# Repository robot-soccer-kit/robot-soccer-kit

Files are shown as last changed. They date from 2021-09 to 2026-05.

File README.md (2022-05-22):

# Robot Soccer Kit

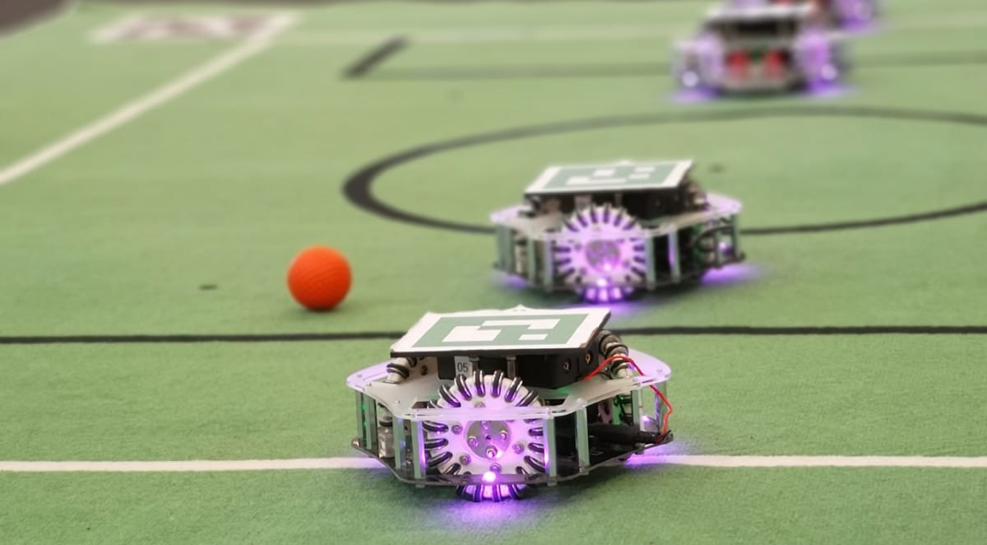
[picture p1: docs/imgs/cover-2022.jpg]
Robots


## Presentation

* [YouTube demonstration video](https://www.youtube.com/watch?v=4NFXbaom7YQ)
* [Documentation](https://robot-soccer-kit.github.io)

## License

<br />This work is licensed under a <a rel="license" href="http://creativecommons.org/licenses/by-nc/2.0/">Creative Commons Attribution-NonCommercial 2.0 Generic License</a>.

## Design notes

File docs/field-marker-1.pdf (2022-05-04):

## Marker 1

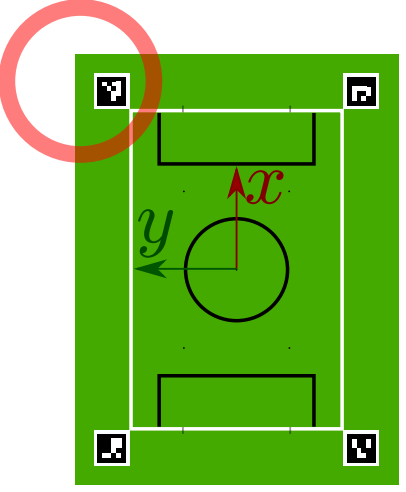
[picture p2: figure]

## WARNING

Use the same position and
orientation as on the picture

Keep ~2.5 cm of white around the marker

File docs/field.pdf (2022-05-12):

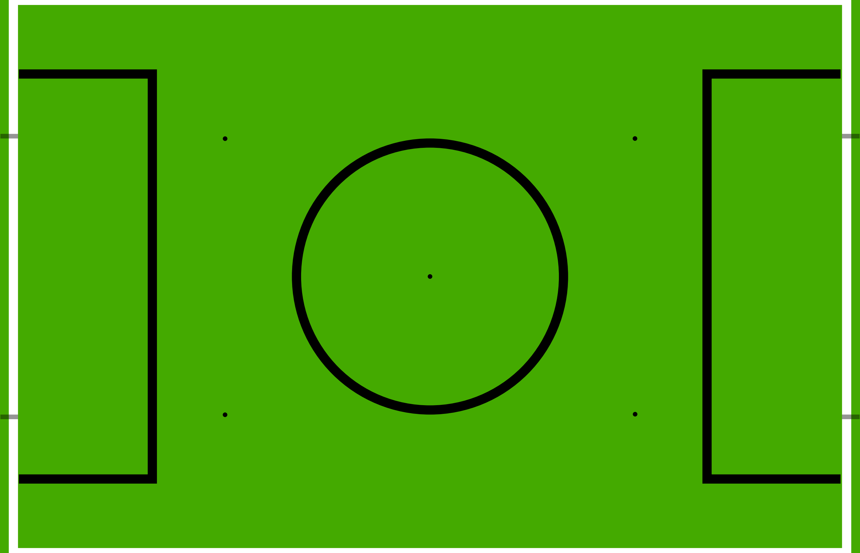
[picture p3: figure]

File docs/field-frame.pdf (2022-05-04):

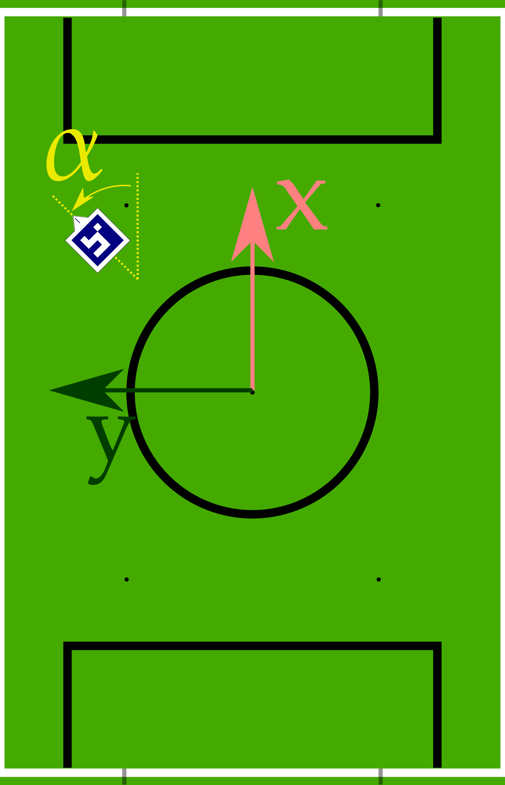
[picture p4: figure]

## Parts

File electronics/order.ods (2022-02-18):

Item # | Ref | Qty | Manufacturer | Mfg Part # | Description | Package | Type | Instruction
1 | B1 | 1 |  |  | BUZZER66 |  |  | CEM-1203
2 | C1, C2, C3, C4, C5, C6, C7, C8 | 8 |  |  | 0.1µF |  |  | 2688486RL
3 | C10, C11 | 2 |  |  | 47pF |  |  | 1081223
4 | C15, C16 | 2 |  |  | 22uF |  |  | 2666560
5 | C19, C20 | 2 |  |  | 2200uF |  |  | 1902893
6 | D1 | 1 |  |  | PMEG4030EP |  |  | 1829201
7 | D3 | 1 |  |  |  |  |  | 8737843RL
8 | J1 | 1 |  |  | USB-B |  |  | 1308876
9 | J2 | 1 |  |  |  |  |  | 1217037
10 | J3, J4, J5 | 3 |  |  | B6B-ZR |  |  | 9491805
11 | J6 | 1 |  |  | KICKER |  |  | JF-0530B
12 | L1 | 1 |  |  | IHLP2525CZER220M11IND_IHLP_2525_CZ_VIS-M |  |  | 1741369
13 | LED1, LED2, LED3, LED4, LED5, LED6 | 6 |  |  | WS2812B5050 |  |  | WS2812B 5050
14 | Q1, Q2 | 2 |  |  | IRLMS2002TRPBF |  |  | 2577180RL
15 | Q3 | 1 |  |  | NPN_BC817,215 |  |  | 1081223
16 | Q4 | 1 |  |  | SUD50N04-8M8P-4GE3 |  |  | 1794799
17 | R1 | 1 |  |  | 270 |  |  | 1887603
19 | R3 | 1 |  |  | 20K |  |  | 2074395
20 | R4 | 1 |  |  | 68k |  |  | 2447023
21 | R5, R9, R10 | 3 |  |  | 10K |  |  | 2074334RL
22 | R6 | 1 |  |  | 3K |  |  | 2447648
23 | R7 | 1 |  |  | 470 |  |  | 2447662
24 | R2, R8, R11 | 3 |  |  | 2K |  |  | 2447622
25 | R12, R13 | 2 |  |  | 22 |  |  | 2446926
26 | REG1 | 1 |  |  | REG 3.3V |  |  | 3470633
 | REG2 | 1 |  |  | REG 5V |  |  | 3470634
27 | S1 | 1 |  |  | DPDT |  |  | 2435159
28 | U1 | 1 |  |  | FT232L |  |  | 1146032
29 | U2 | 1 |  |  | ESP32-WROOM-32E_(16MB) |  |  | ESP32-WROOM
30 | U3 | 1 |  |  | S8252 |  |  | https://www.digikey.fr/fr/products/detail/ablic-u-s-a-inc/S-8252AAL-M6T1U/6121452
31 | U4, U5, U6 | 3 |  |  | L9110 |  |  | L9110 SOIC8
32 | U7 | 1 |  |  | MT3608 |  |  | MT3608

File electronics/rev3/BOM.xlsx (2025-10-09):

Item # | Ref | Qty | Manufacturer | Mfg Part # | Description | Package | Type | Instruction
1 | R2 | 1 | MULTICOMP PRO | MCSR08X2001FTL | 2k ohms | R0805 | SMD
2 | R3 | 1 | MULTICOMP PRO | MCSR08X2002FTL | 20k ohms | R0805 | SMD
3 | R4, R18 | 2 | MULTICOMP PRO | MCWR08X6802FTL | 68k ohms | R0805 | SMD
4 | R1, R5, R16, R17 | 4 | MULTICOMP PRO | MCSR08X1002FTL | 10k ohms | R0805 | SMD
5 | R6 | 1 | MULTICOMP PRO | MCWR08X3001FTL | 3k ohms | R0805 | SMD
6 | R7, R9, R10 | 3 | MULTICOMP PRO | MCWR08X4700FTL | 470 ohms | R0805 | SMD
7 | R8, R11 | 2 | MULTICOMP PRO | MCWR08X2001FTL | 2k ohms | R0805 | SMD
8 | R12, R13 | 2 | MULTICOMP PRO | MCWR08X22R0FTL | 22 ohms | R0805 | SMD
9 | R15, R22 | 2 | MULTICOMP PRO | MCWR08X5101FTL | 5.1k ohms | R0805 | SMD
10 | R14 | 1 | MULTICOMP PRO | MCPWR10FTEQ2700 | Kicker resistor (270) | R2010 | SMD
11 | R19 , R20, R21 | 3 | VISHAY | RCWE0805R330FKEA | 330 mOhms | R0805 | SMD
12 | C13, C17, C18, C21, C22 | 5 | MURATA | GCM21BR71E105KA56L | 1µF | C0805 | SMD
13 | C1, C2, C3, C4, C5, C6, C7, C8, C9, C12, C14 | 11 | MURATA | GCM21BR72A104KA37K | 0.1µF | C0805 | SMD
14 | C10, C11 | 2 | MULTICOMP PRO | MC0805N470J500CT | 47pF (USB) | C0805 | SMD
15 | C15, C16 | 2 | MURATA | GRM21BR61E226ME44L | 22uF (Booster) | C0805 | SMD
16 | C19, C20 | 2 | WURTH ELEKTRONIK | 860020478022 | 2200uF 25V capacitors (Kicker) |  | Thru-holes
17 | D1 | 1 | NEXPERIA | PMEG4030EP,115 | Kicker diode | SOD-128 | SMD
18 | D2, D3 | 2 | NEXPERIA | PMEG2005AEA,115 | USB diode, BMS bootstrap polarity protection diode | SOD-323 | SMD
19 | B1 | 1 | CUI Devices | CEM-1203 | Buzzer |  | Thru-holes
20 | J1 | 1 | MULTICOMP PRO | USB-B-S-RA | USB Connector |  | Thru-holes
21 | J2 | 1 | MULTICOMP PRO | MJ-180PH | Jack 2.5mm « barrel » connector |  | Thru-holes
22 | J3, J4, J5 | 3 | JST (JAPAN SOLDERLESS TERMINALS) | B6B-ZR(LF)(SN) | JST XH 6p |  | Thru-holes
23 | J6 | 1 |  | JF-0530B | Solenoid Kicker |  | SMD | DO NOT MOUNT
24 | L1 | 1 | VISHAY | IHLP2525CZER220M11 | Kicker booster inductance |  | SMD
25 | LED1, LED2, LED3, LED4, LED5, LED6 | 6 | SparkFun | COM-16346 | RGB LEDs (WS2812B) |  | SMD
26 | Q1, Q2, Q7 | 3 | INFINEON | IRLMS2002TRPBF | BMS Mosfet |  | SMD
27 | Q3, Q5, Q6 | 3 | NEXPERIA | BC817,215 | NPN Transistor |  | SMD
28 | Q4 | 1 | MCC (MICRO COMMERCIAL COMPONENTS) | MCU60N04A-TP | Kicker MOSFET |  | SMD
29 | REG1 | 1 | TRACO POWER | TSR 1-2450E | 5V regulator (switching) |  | Thru-holes
30 | U8 | 1 | ANALOG DEVICES | LT1963AEST-3.3#PBF | 3.3V regulator (LDO) |  | SMD
31 | SW1 | 1 | C&K COMPONENTS | L102011ML04Q | Main switch (SPDT) |  | Thru-holes
32 | U1 | 1 | FTDI | FT232RL-REEL | USB 2 UART (FTDI) |  | SMD
33 | U2 | 1 | ESPRESSIF SYSTEMS | ESP32-WROOM-32E-N8 | MCU ESP32 |  | SMD
34 | U3 | 1 | ABLIC Inc. | S-8252AAL-M6T1U | BMS |  | SMD
35 | U10, U11, U12 | 3 | TOSHIBA | TB67H450FNG,EL | H-bridge | SOP8 | SMD
36 | U7 | 1 | AEROSEMI | MT3608 | Step-up Booster 20V |  | SMD
37 | D4 | 1 | ONSEMI | RS1M | Kicker free wheel diode |  | SMD

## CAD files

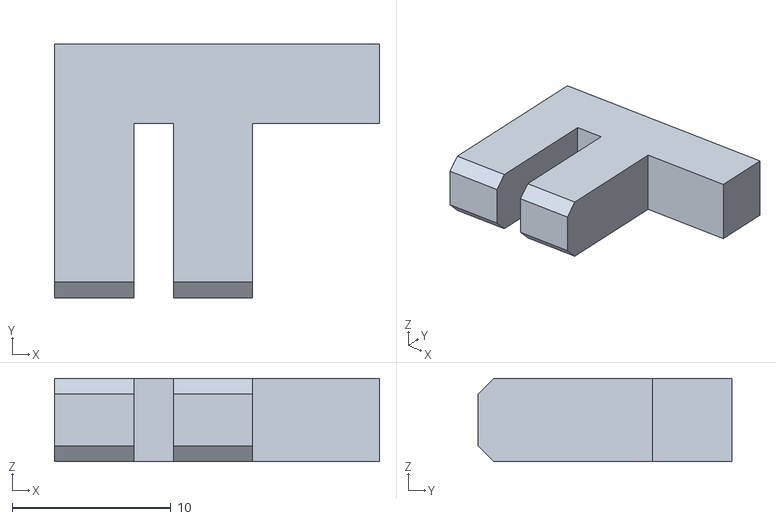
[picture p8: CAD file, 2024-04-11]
mechanics/blocker.stl
20.5 x 16.0 x 5.25

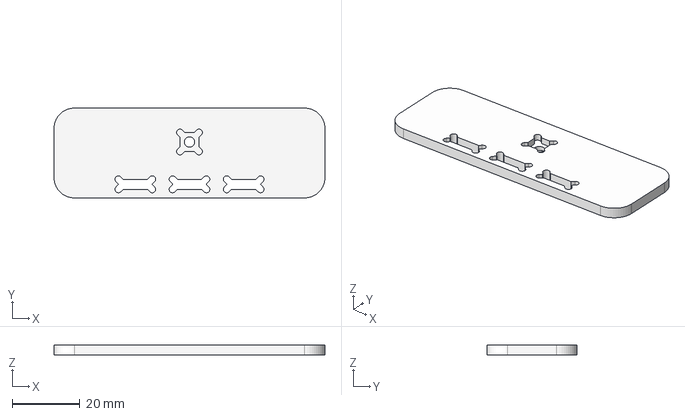
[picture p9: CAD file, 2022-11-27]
mechanics/kicker_tip_1.step
80.0 x 26.5 x 3.00 mm

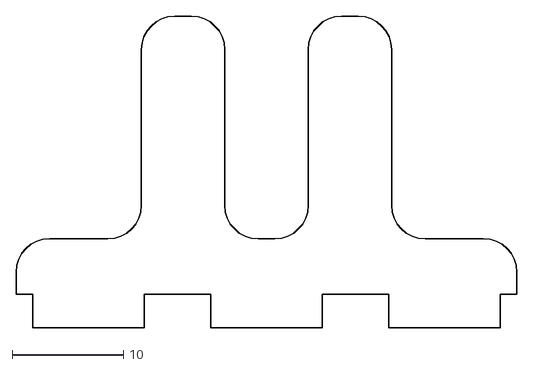
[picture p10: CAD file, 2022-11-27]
mechanics/kicker_tip_2.dxf
45.0 x 28.0

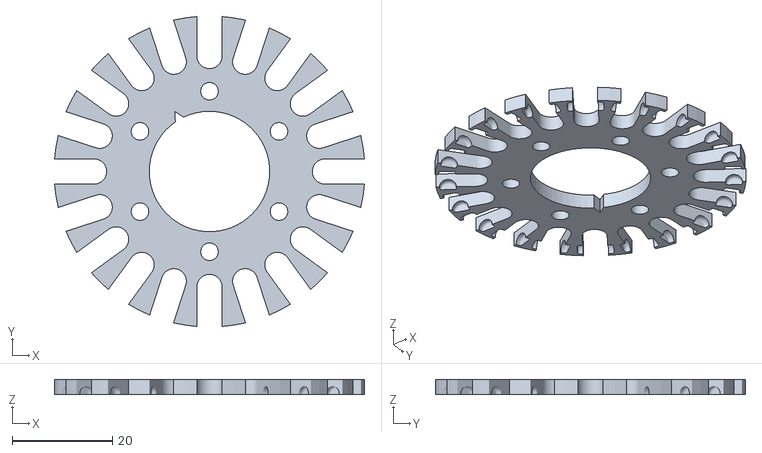
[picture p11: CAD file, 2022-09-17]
mechanics/wheel2.stl
61.8 x 61.8 x 3.00

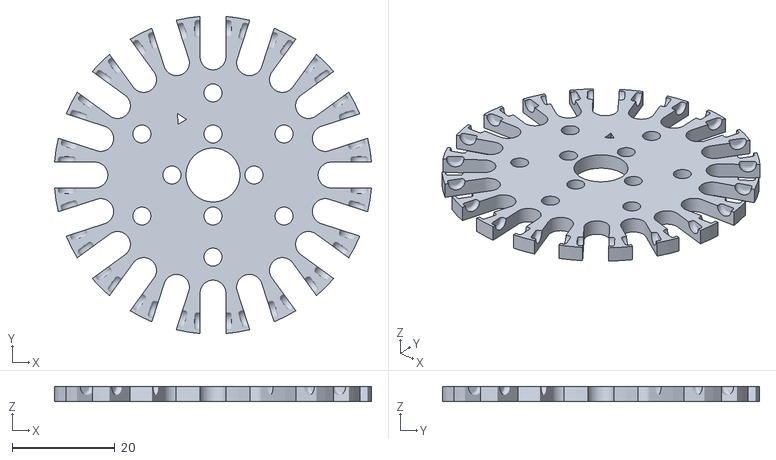
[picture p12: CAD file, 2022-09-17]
mechanics/wheel1.stl
61.8 x 61.8 x 3.00

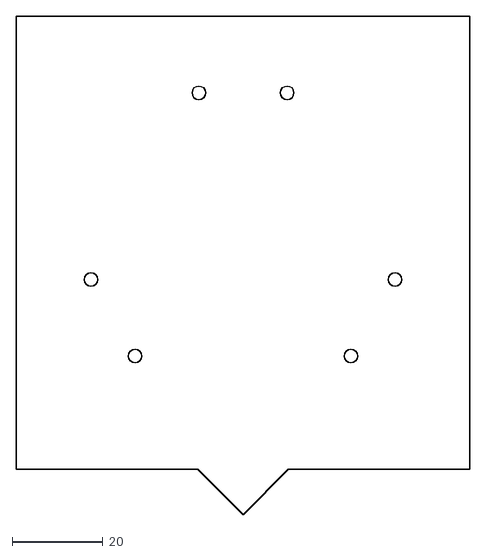
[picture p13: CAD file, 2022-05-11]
mechanics/marker.dxf
100.0 x 110.0

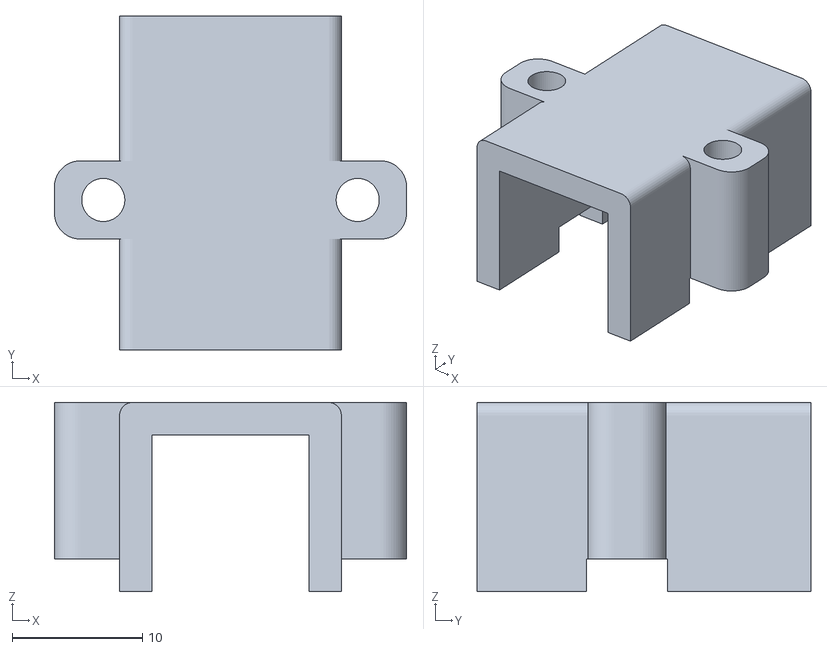
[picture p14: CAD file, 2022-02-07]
mechanics/motorbox_top.stl
27.0 x 25.6 x 14.5

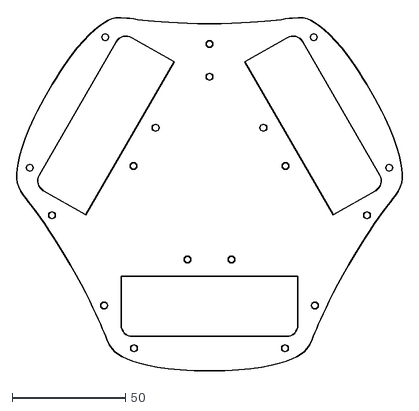
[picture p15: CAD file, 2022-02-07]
mechanics/electronics_board.dxf
170.6 x 156.5

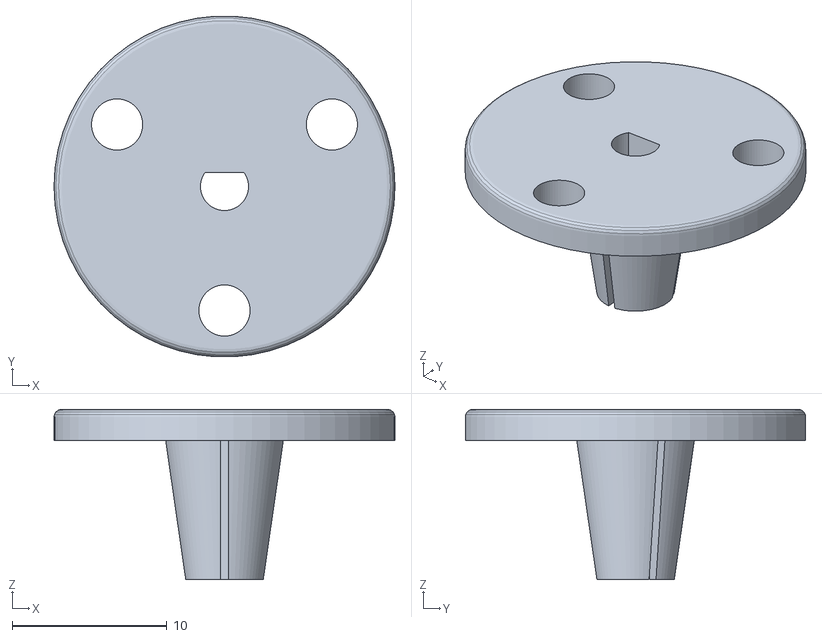
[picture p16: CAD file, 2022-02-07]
mechanics/coupler.stl
22.0 x 22.0 x 11.0

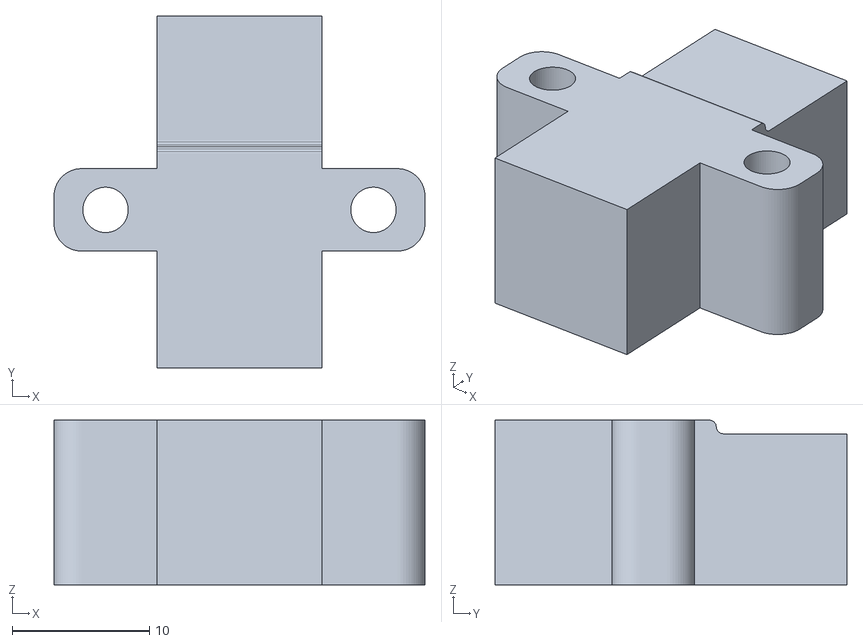
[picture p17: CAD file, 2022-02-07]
mechanics/motorbox_bottom.stl
27.0 x 25.6 x 12.0

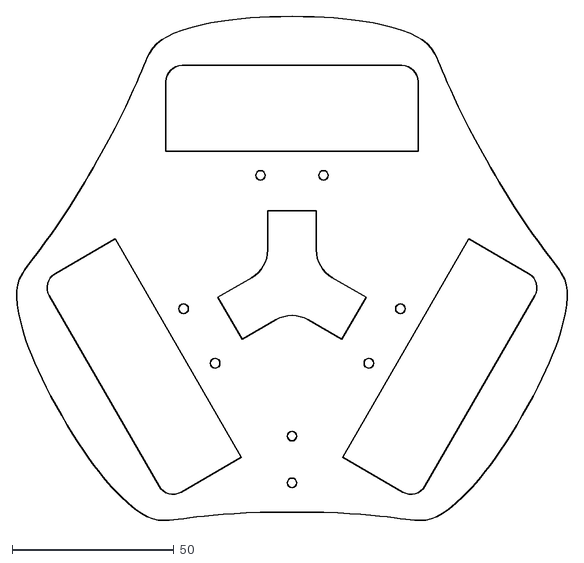
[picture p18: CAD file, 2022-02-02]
mechanics/frame.dxf
170.6 x 156.5

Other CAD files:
mechanics/kicker_tip_1.dxf

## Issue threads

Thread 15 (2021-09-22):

Robots upgrade and rework

Gregwar, 2021-09-22:
Branch `electronics_rework`

- [x] Use 18650 instead of embedded lithium ion (the coupler should fit in current robots)
  - In this move, a way much simpler switch can be used because embedded charge would not be needed anymore
  - Maybe we can have a DC 5.5mm connector and use a coupler
- [x] Get the robot closer to the ground (by ~5mm)
- [x] Remove buttons
- [x] Remove connectors for optical sensors
- [x] Remove distance sensor
- [x] Remove useless multiplexers
- [x] Merge the kicker board to the robot's PCB itself
- [x] Get the robot shielded against collisions (avoid overlap)
- [x] Change the kicker tip (make it wider and more concave)

Ideas / questions
- Can we switch to another reduction ratio ?
- Can we remove the IMU ?
- Should we still use HC-05 or switch to something else ? (Test other bluetooth modules)

Closed 2022-05-04.

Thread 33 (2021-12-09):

When a robot blinks because of battery error and goes back to normal, LED are not re-set to marker's

Gregwar, 2021-12-09:

Closed 2022-05-22.

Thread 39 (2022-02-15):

Electronics rework remarks

Gregwar, 2022-02-15:
- [ ] VM needs to be shorted after battery was plugged

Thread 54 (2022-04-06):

Undefined behavior with the Bluetooth pairing

CoAuToSe, 2022-04-06:
When connecting one of the robots with Bluetooth, the robot almost imediatly change from "connected" to "coupled". Therefore, we can't properly use the robots. The physical setup used is this [one](https://robot-soccer-kit.github.io/hardware-setup) and the software setup is this [one](https://robot-soccer-kit.github.io/install-windows/) (the software is working properly when the robot is "connected" but not "coupled"), meaning that it should be working but it doesn't... We got it working properly about 1 time out of 30 (mainly with a new computer each try but also rarely with one that was already used).

Also, when looking at the Device Manager, the robot is still in the Bluetooth device (even shutdown) and doesn't want to be deleted, but can be deleted when there are multiple robot. (example: I have "holo_6" in my list of Bluetooth devices but the robot "holo_6" is 2 km away from me and is not powered)

OS: Windows 10

Gregwar, 2022-04-06:
Hello,

1. Is there internal Bluetooth in the computers you are using ?
2. If you want to delete a robot, can you try plugging the dongle you used for pair before clicking on "Delete" ?

I am not sure to understand what your problem actually is; do you mean that COM ports opening simply fails?

CoAuToSe, 2022-04-06:
There is internal Bluetooth in the computers we use. We started using it because it was able to "work" but we bought a dongle and nothing changed when using it.
We initially paired the robot with the Bluetooth of our computers and not with the dongle. When we tried to pair them with the dongle, we ran into the same issue.

We can delete the COM ports as much as we want, but I think that the Bluetooth pairing is not working as intended in our case as. We can connect to the robots with Bluetooth without issue (creating the COM ports) but the connection seems to be unstable, usually ending in pairing and not conneting. And, therefore, not allowing us to use the robots.

cgaspard3333, 2022-04-06:
Hello,

We are trying to understand your problem.
Are you a student or a teacher participating to the RSK program in the "Académie de Bordeaux" ?

If so, we can help you with a TeamViewer assistance.
We have the setup fully working with several Computers with Windows 10 and Windows 11 and no real pairing problem (most of the time this sort of problem apears on Linux)

However, using the internal Bluetooth is not really fonctionnal. For now, we strongly recommand to use a dongle.
(It works well with the following dongle referenced in the documentation : ZEXMTE Adaptateur Bluetooth Usb 5.0)
By experiment, Realtek internal Bluetooth seems to work, but Intel is not working well.

Furthermore, **before plugging in the dongle** (and then use it), you have to first disable the internal Bluetooth adapter **in the Device Manager** and not in the Windows Settings interface. Then try to pair again the bots (even they already exist in the device manager)

CoAuToSe, 2022-04-15:
Ok, so I resolved the problem that I was having but it came back later with the dongle, here is how I handled the issues:

1. First, I had the problem with the Bluetooth of the computer taking the lead over the dongle, which may create some Bluetooth ghost linked Robot (which can't be deleted). It was solved by disalbing the Bluetooth of the computer and then plugging in the dongle which may allow the ghost linked robots to be deleted. Otherwise it is the second problem that I resolved.

2. I ran into another problem when coming back to my "old" workspace, about one week without working with it. All the robot's Bluetooth links became ghost on the dongle's Bluetooth and didn't wanted to be deleted(even with the dongle plugged in in the right USB).
To resolve it, I came back to a fresh state of the computer that I was using. I tried deleting Bluetooth links as soon as possible (if u don't use the dongle it may not work, as tested) but there was one ghost robot remaining (and the game controller wasn't working as intended). I might have tried everything that would come to mind quickly to solve this issues.
The solution that I found was to unplug the dongle and reactivate my computer's Bluetooth followed by a restart of the computer (restarting without the computer's Bluetooth reactivated didn't solved the issue for us, shutting down and turning on the computer wasn't tested). Which allowed the deletion of the ghost robot when plugging the dongle (may require to be done "as fast as possible", otherwise you may need to restart "the whole solution"). Therefore it was as if I had never connected the robots to the computer. Following with the steps of the first issue, we currently have it working for us. (even if I had to wait more than a minute "in the void" for the robot to connect with the game controller, with the dongle plugged and a robot linked with the Blutooth)

I also recognised that the dongle may need to be plugged into a USB type charger(the one with the charger icon) of a laptop to have it working. The dongle's LED was blinking more when used this way, and I had more problems otherwise.

The process are long and may be shortened.

To clarify who I am, I am Aurelien from ESME.

Closed 2022-04-30.

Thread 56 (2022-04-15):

Camera calibration

Gregwar, 2022-04-15:
Instead of computing an homography, we could estimate intrinsic+extrinsic camera parameters.
That would give more convenient tool to compute the projection of objects that doesn't lie in the ground plane.

Closed 2022-05-04.

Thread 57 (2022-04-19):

Electronics rev1

Gregwar, 2022-04-19:
- Board should be re-routed: the decoupling capacitor of U5 is too far
- Add 1uF decoupling on H-bridges
- We broke some L9110, but it is likely to come from a bad batch, we might switch to a more reliable H driver

Closed 2022-11-14.

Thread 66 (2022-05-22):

Dispatch to robot to different penalty locations

Gregwar, 2022-05-22:
Currently when a robot is penalized it is just sent to the current X position and the closest border for Y, we could pre-allocate penalty locations around the field and send the robot to the closest unoccupied one, avoiding robots stacking together when penalized

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

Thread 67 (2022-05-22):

Set a limit of time between 2 kicks

Gregwar, 2022-05-22:
In the firmware, that would ensure capacitors reloaded before kicking again. Since it doesn't look like to damage anything that is not affecting the games that much so far though and is debatable.

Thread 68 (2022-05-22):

Removing penalties when placing the robots?

Gregwar, 2022-05-22:
Currently, when there is a lack of progress, we click "Pause" and then "Standard" and then "Resume"; but this doesn't remove the robots penalties (as an effect, the robot goes back to its penalized area after placing)

I suggest that clicking "Standard" remove the robots penalties, since I think it would solve this use case and doesn't seems to affect other use cases.

Closed 2022-11-14.

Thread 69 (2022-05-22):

Swapping covers robots placement

Gregwar, 2022-05-22:
We don't know if the robots finished their placing when swapping covers, it can happen that they didn't and taking their cover in this situation is very annoying

I don't know what to do to solve this, maybe having a way to know if they are moving or ready to swap (LEDs?)

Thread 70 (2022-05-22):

Client exceptions management

Gregwar, 2022-05-22:
Client exceptions `ClientError` are currently raised when:
1. The key is bad
2. The team is not allowed to control robots
3. The robot is preempted
4. The robot is penalized (which is actually a sub-case of preempted)

Cases 1., 2. and 3.+4. should be easily programmatically distinguishable using maybe a different exception.

Also, since most teams simply ignore the errors with a `pass` (at least when preempted/penalized), it should be possible to simply silently ignore them, for instance `client.raise_exceptions = False` to disable exceptions for cases 2.+3.+4.

I think case 1. should always raise though.

Maybe we should have 3 levels instead, like `client.error_management = "..."`, with `"ignore"`, `"print"` and `"raise"` (default: print)

Gregwar, 2022-06-07:
If we disable exception, we could call it yoda mode :-)

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

Closed 2023-04-07.

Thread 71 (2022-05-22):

Robot restarts when opening connection

Gregwar, 2022-05-22:
Sometime when opening the connection with robots, they restart. We are not sure yet why this happens. It is not causing a big problem since when the connection is successful we didn't observe any problem during the competition.

Observed from Ubuntu 22.04 main computer.

Here are some hypotheses but the problem needs to be reproduced and investigated further:
- Maybe it is because the batteries voltage is too high (+8V) and the BMS over-voltage shut-down
- Maybe it is because something is trying to send orders to the robot (tasks or clients through API) at the same time

Gregwar, 2022-11-14:
Duplicates #86

Closed 2022-11-14.

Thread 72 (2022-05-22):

Timer should be reset to 05:00 before we click on Resume

Gregwar, 2022-05-22:
Currently it shows the timer from the previous game, and only resets to 05:00 when game actually starts

Closed 2023-04-07.

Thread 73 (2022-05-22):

Kickers seems irregular from robot to robot

Gregwar, 2022-05-22:
We need to investigate on what makes some robot kicking differently

Leads
- Different Solenoid
- Different mechanics (frictions?)
- Different capacitors
- Different power MOS

We can assemble/disassemble and benchmark, very tedious way to the truth of what really matters here

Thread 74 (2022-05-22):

Robots can't push the ball and can still climb the ball

Gregwar, 2022-05-22:
When the robot move straightfoward to the ball, the kicker gets a little stuck on it. It is not point of the games to push the ball because we want to encourage kicking, but it is still not some behaviour we want.

The kicker is looking "downward" on current builds, we could use a M3 nut to get it looking "upward", we think it would fix this.

Also, the robots can still climb the ball on some situation, maybe the distance between PCB and the ground can be again reduced a little bit.

Gregwar, 2022-11-14:
We think this is caused by the front square nut in the kicker. Should be fixed in design now (to test).

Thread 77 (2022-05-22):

Goals and sideline crossed

Gregwar, 2022-05-22:
In the current code it is possible that both a goal and a sideline crossed is detected simultaneously, it should be exclusive

(Fixed but not commited)

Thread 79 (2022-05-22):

Get wheel closer to motor bearing

Gregwar, 2022-05-22:
Looks like some motors got broken because of radial effort.
The wheels could be mounted closer to the bearing, we think each mm would help reducing this effort. Maybe the wheel can be mounted "inside" the coupler, but we need to be able to access the headless screw for assembling.

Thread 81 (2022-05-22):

Limit motors that force for no result

Gregwar, 2022-05-22:
We don't have temperature feedback, but measure the speed and know the PWM signal used.
If the speed is highly inconsistent with the PWM signal used for too long, we might have some process to stop forcing.

(Maybe a metric like robot "stamina" could be used, to give an incentive to avoid forcing and pushing, and also avoid breaking the motors.)

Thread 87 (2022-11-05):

R19, R20, R21 are not consistent with BOM

Gregwar, 2022-11-05:
R19, R20, R21 (330mOhms) are not consistent between CAD and BOM
BOM is stating R0805 resistors but this is not the package used in the CAD

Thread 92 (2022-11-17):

LEDs and Buzzer in API

Gregwar, 2022-11-17:
- It should be possible, but not during games

Closed 2023-04-07.

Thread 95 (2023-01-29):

Slight adjustements in dimensions

Gregwar, 2023-01-29:
After the last batch, we can slightly adjust:

- [ ] The holes for the upper PMMA plate could be enlarged so that it is less adjusted
- [ ] The holes in the motor box can be enlarged a little bit; the SLS stack pillars sometime fused with it

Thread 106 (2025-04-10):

Timed circle delay

Gregwar, 2025-04-10:
If ball is not seen for a frame, timer seems to be reset
To investigate

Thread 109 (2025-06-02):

Improve robot penalty placement

Gregwar, 2025-06-02:
Currently, the robots often hamper the game when going to penalty spot

Proposal: instead of minimizing distance to penalty spot, avoid intersecting obstacles

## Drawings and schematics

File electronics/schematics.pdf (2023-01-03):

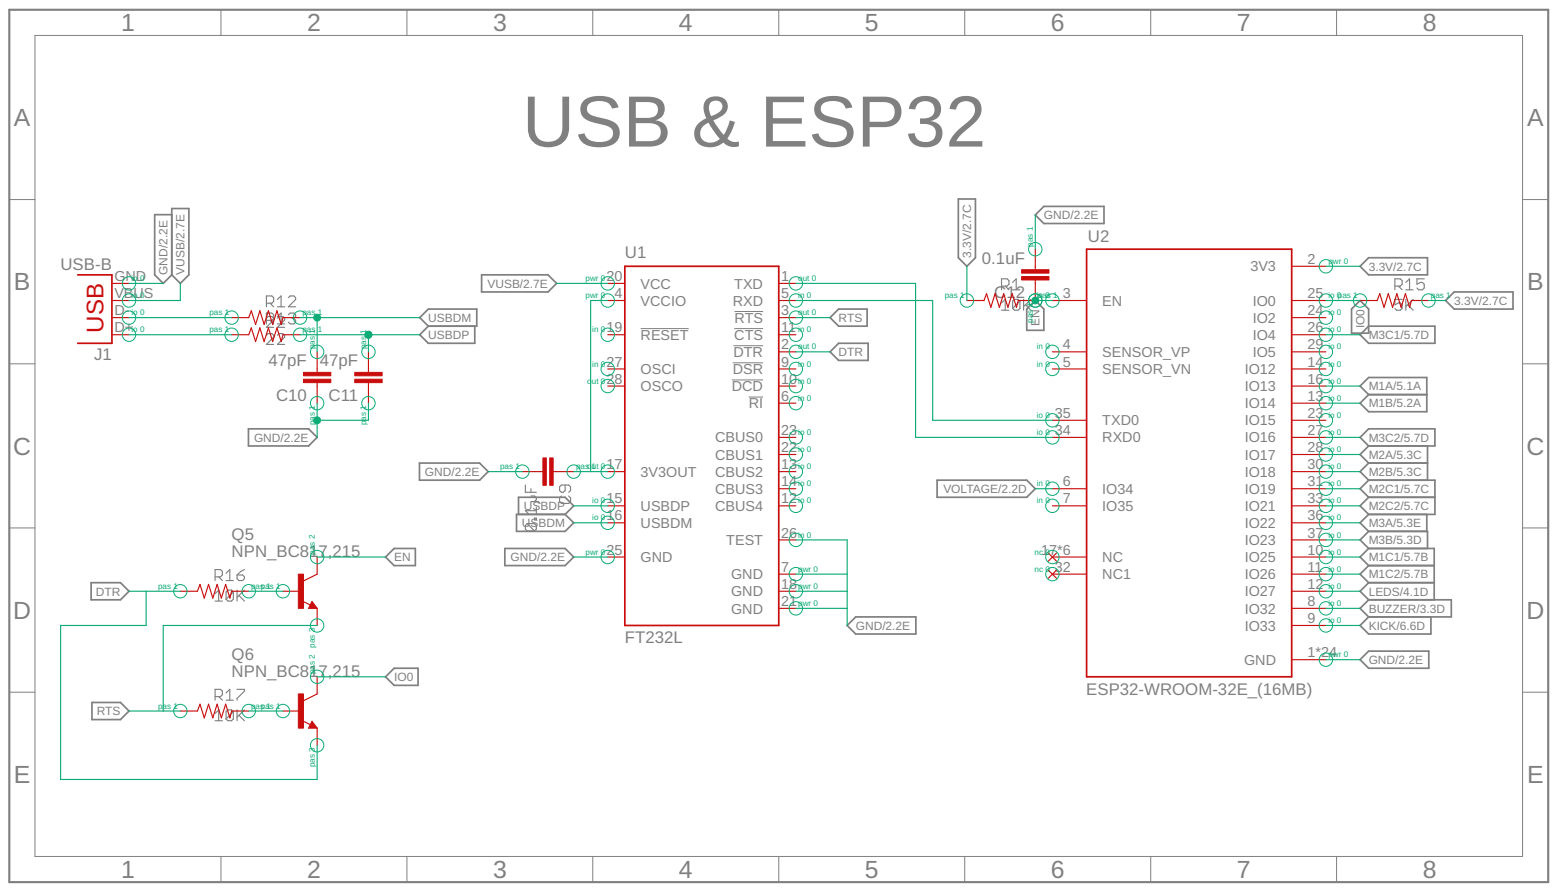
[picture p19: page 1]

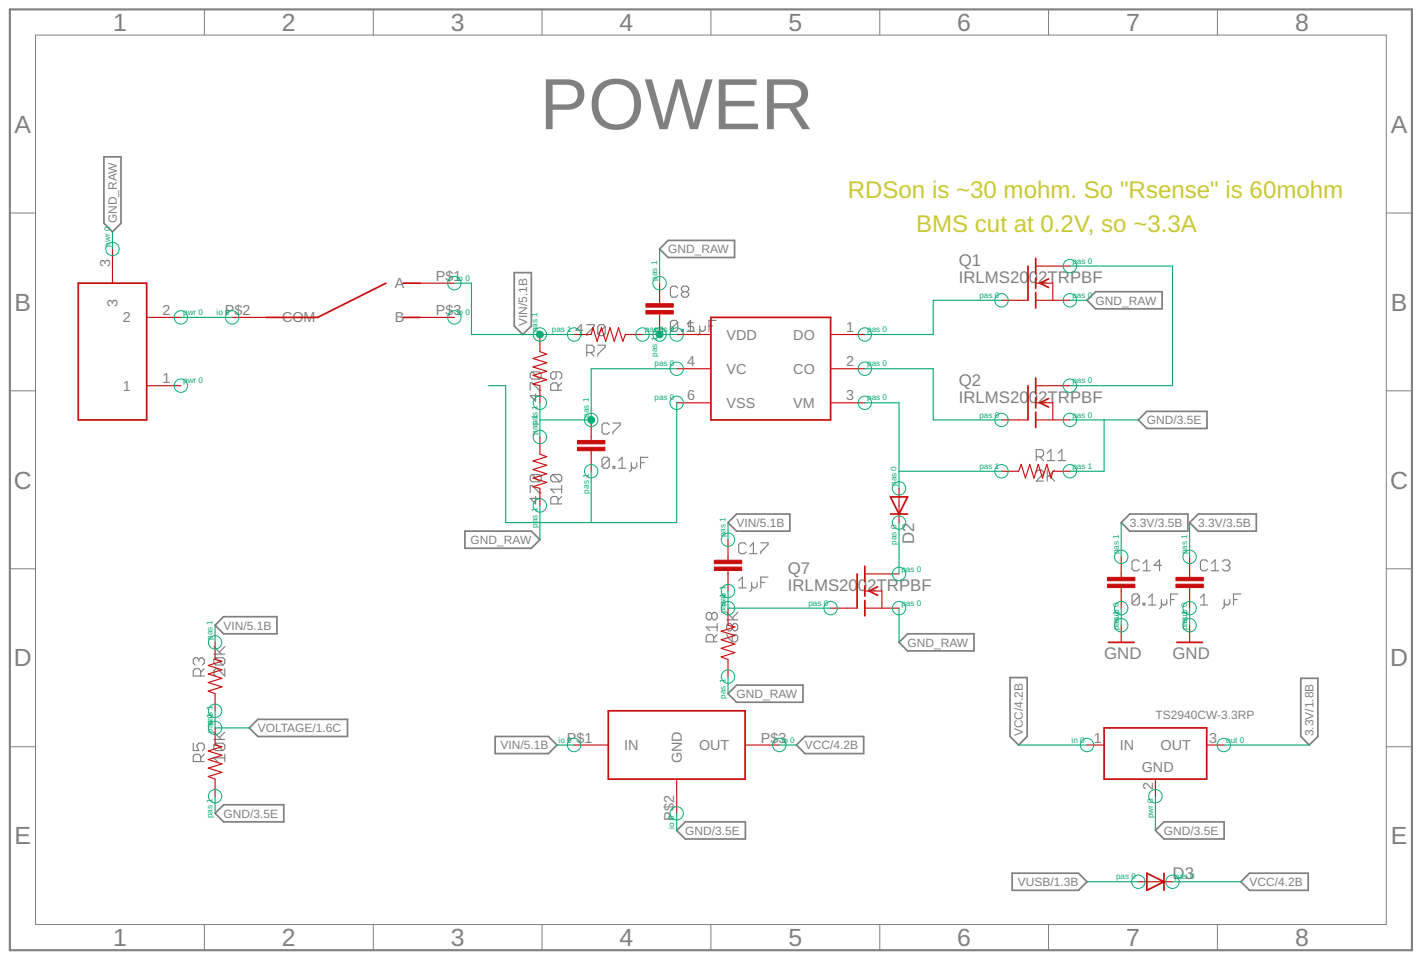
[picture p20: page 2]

POWER

RDSon is ~30 mohm. So "Rsense" is 60mohm
BMS cut at 0.2V, so ~3.3A

pas 1 pas 1

as 1 pas 1 pas 1 pas 1

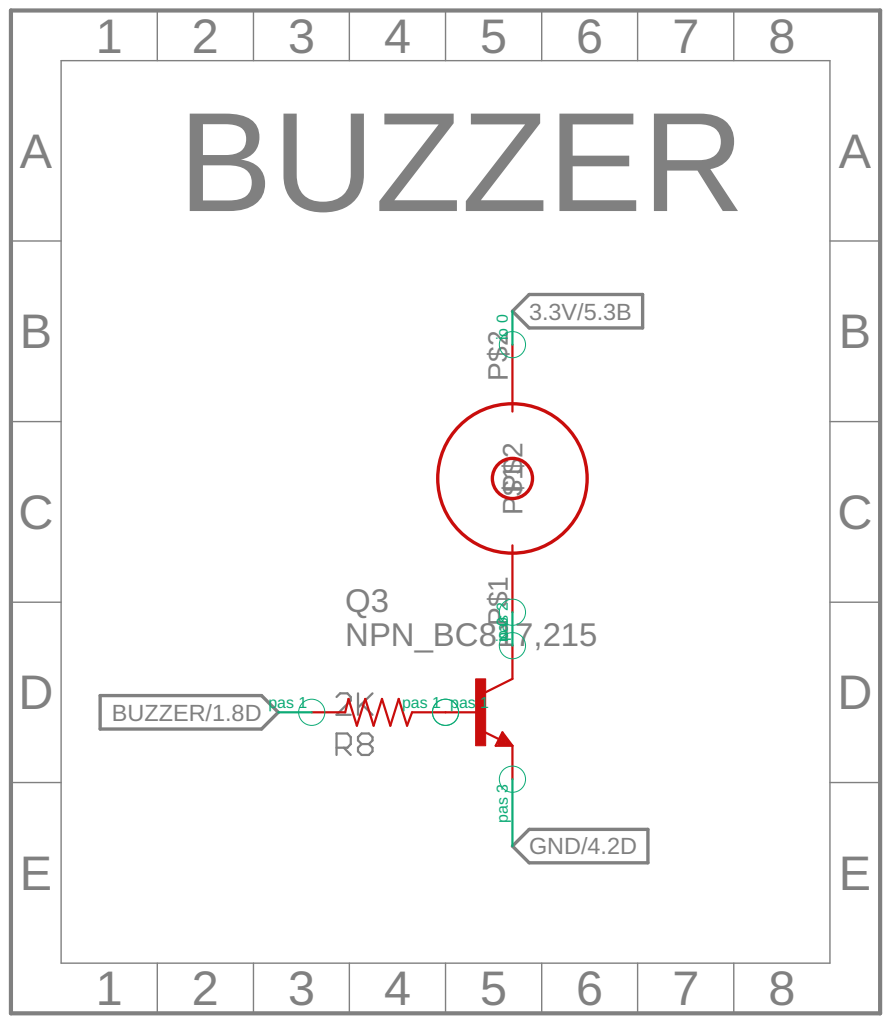
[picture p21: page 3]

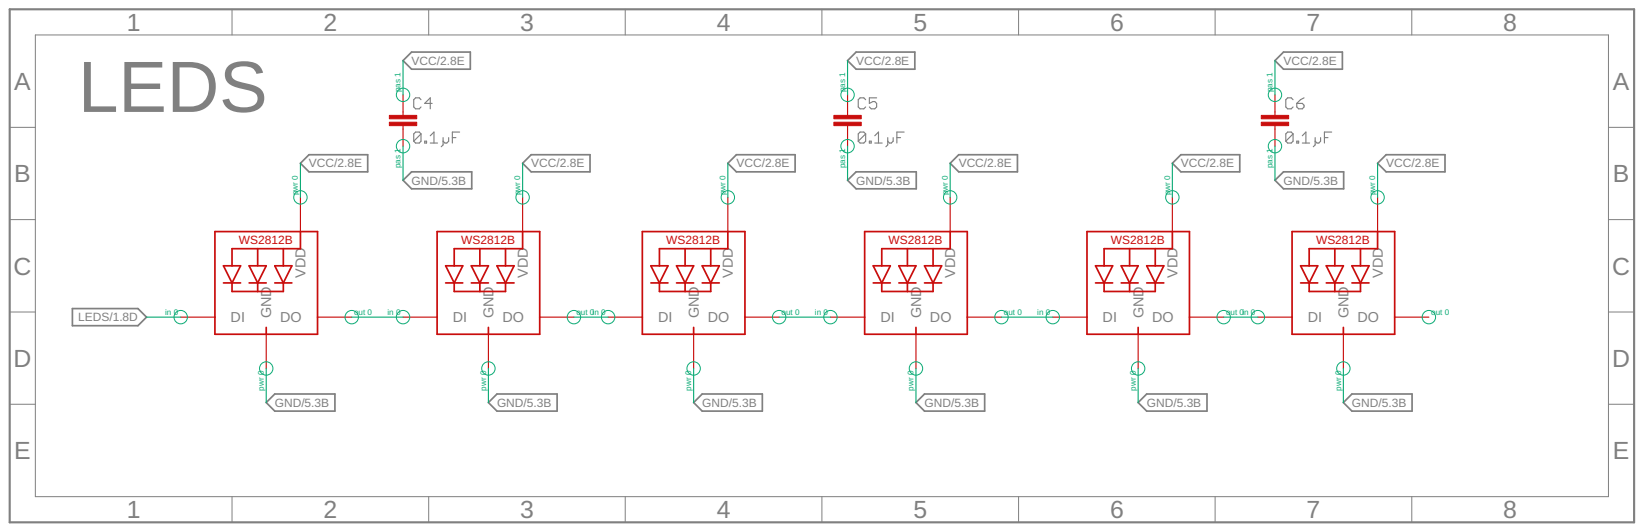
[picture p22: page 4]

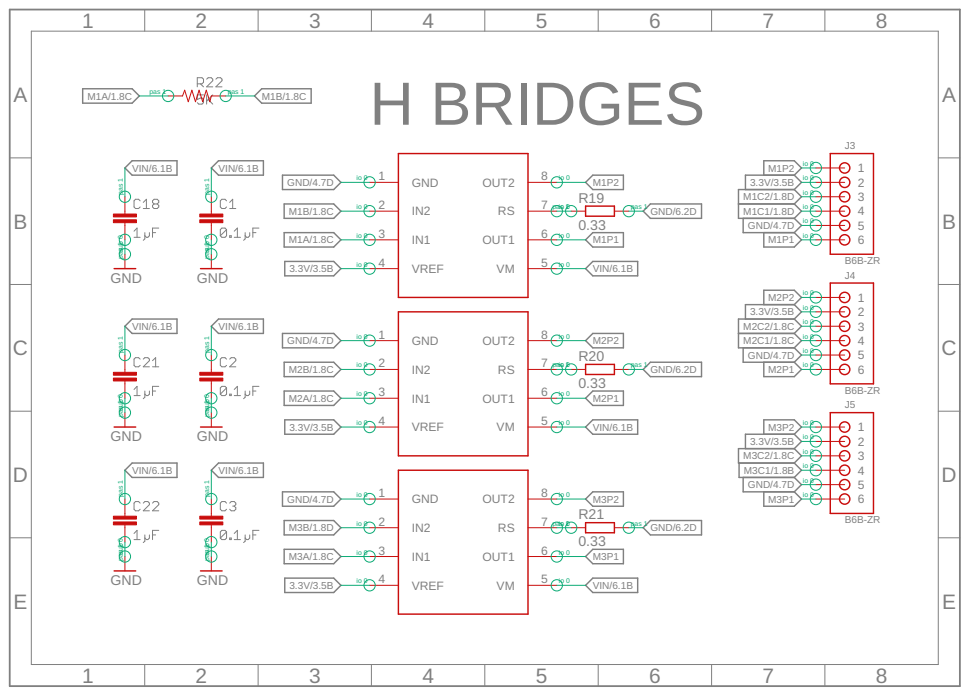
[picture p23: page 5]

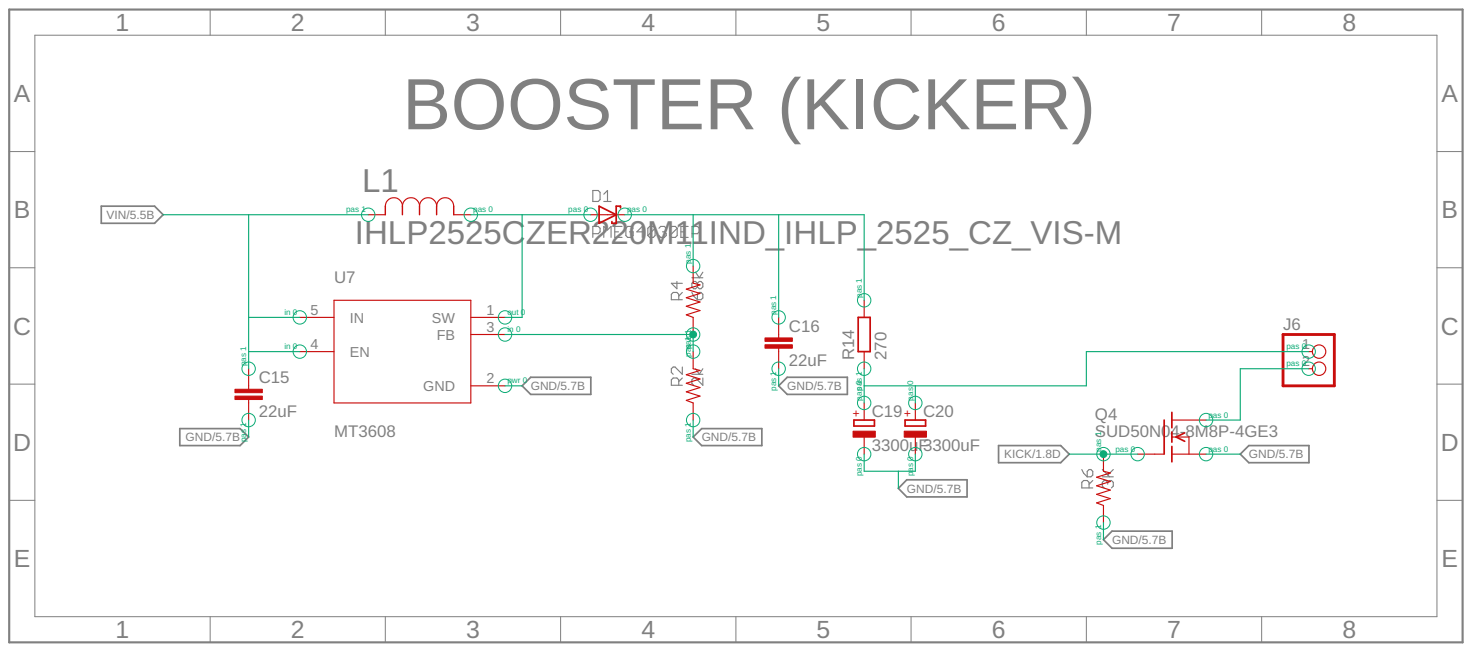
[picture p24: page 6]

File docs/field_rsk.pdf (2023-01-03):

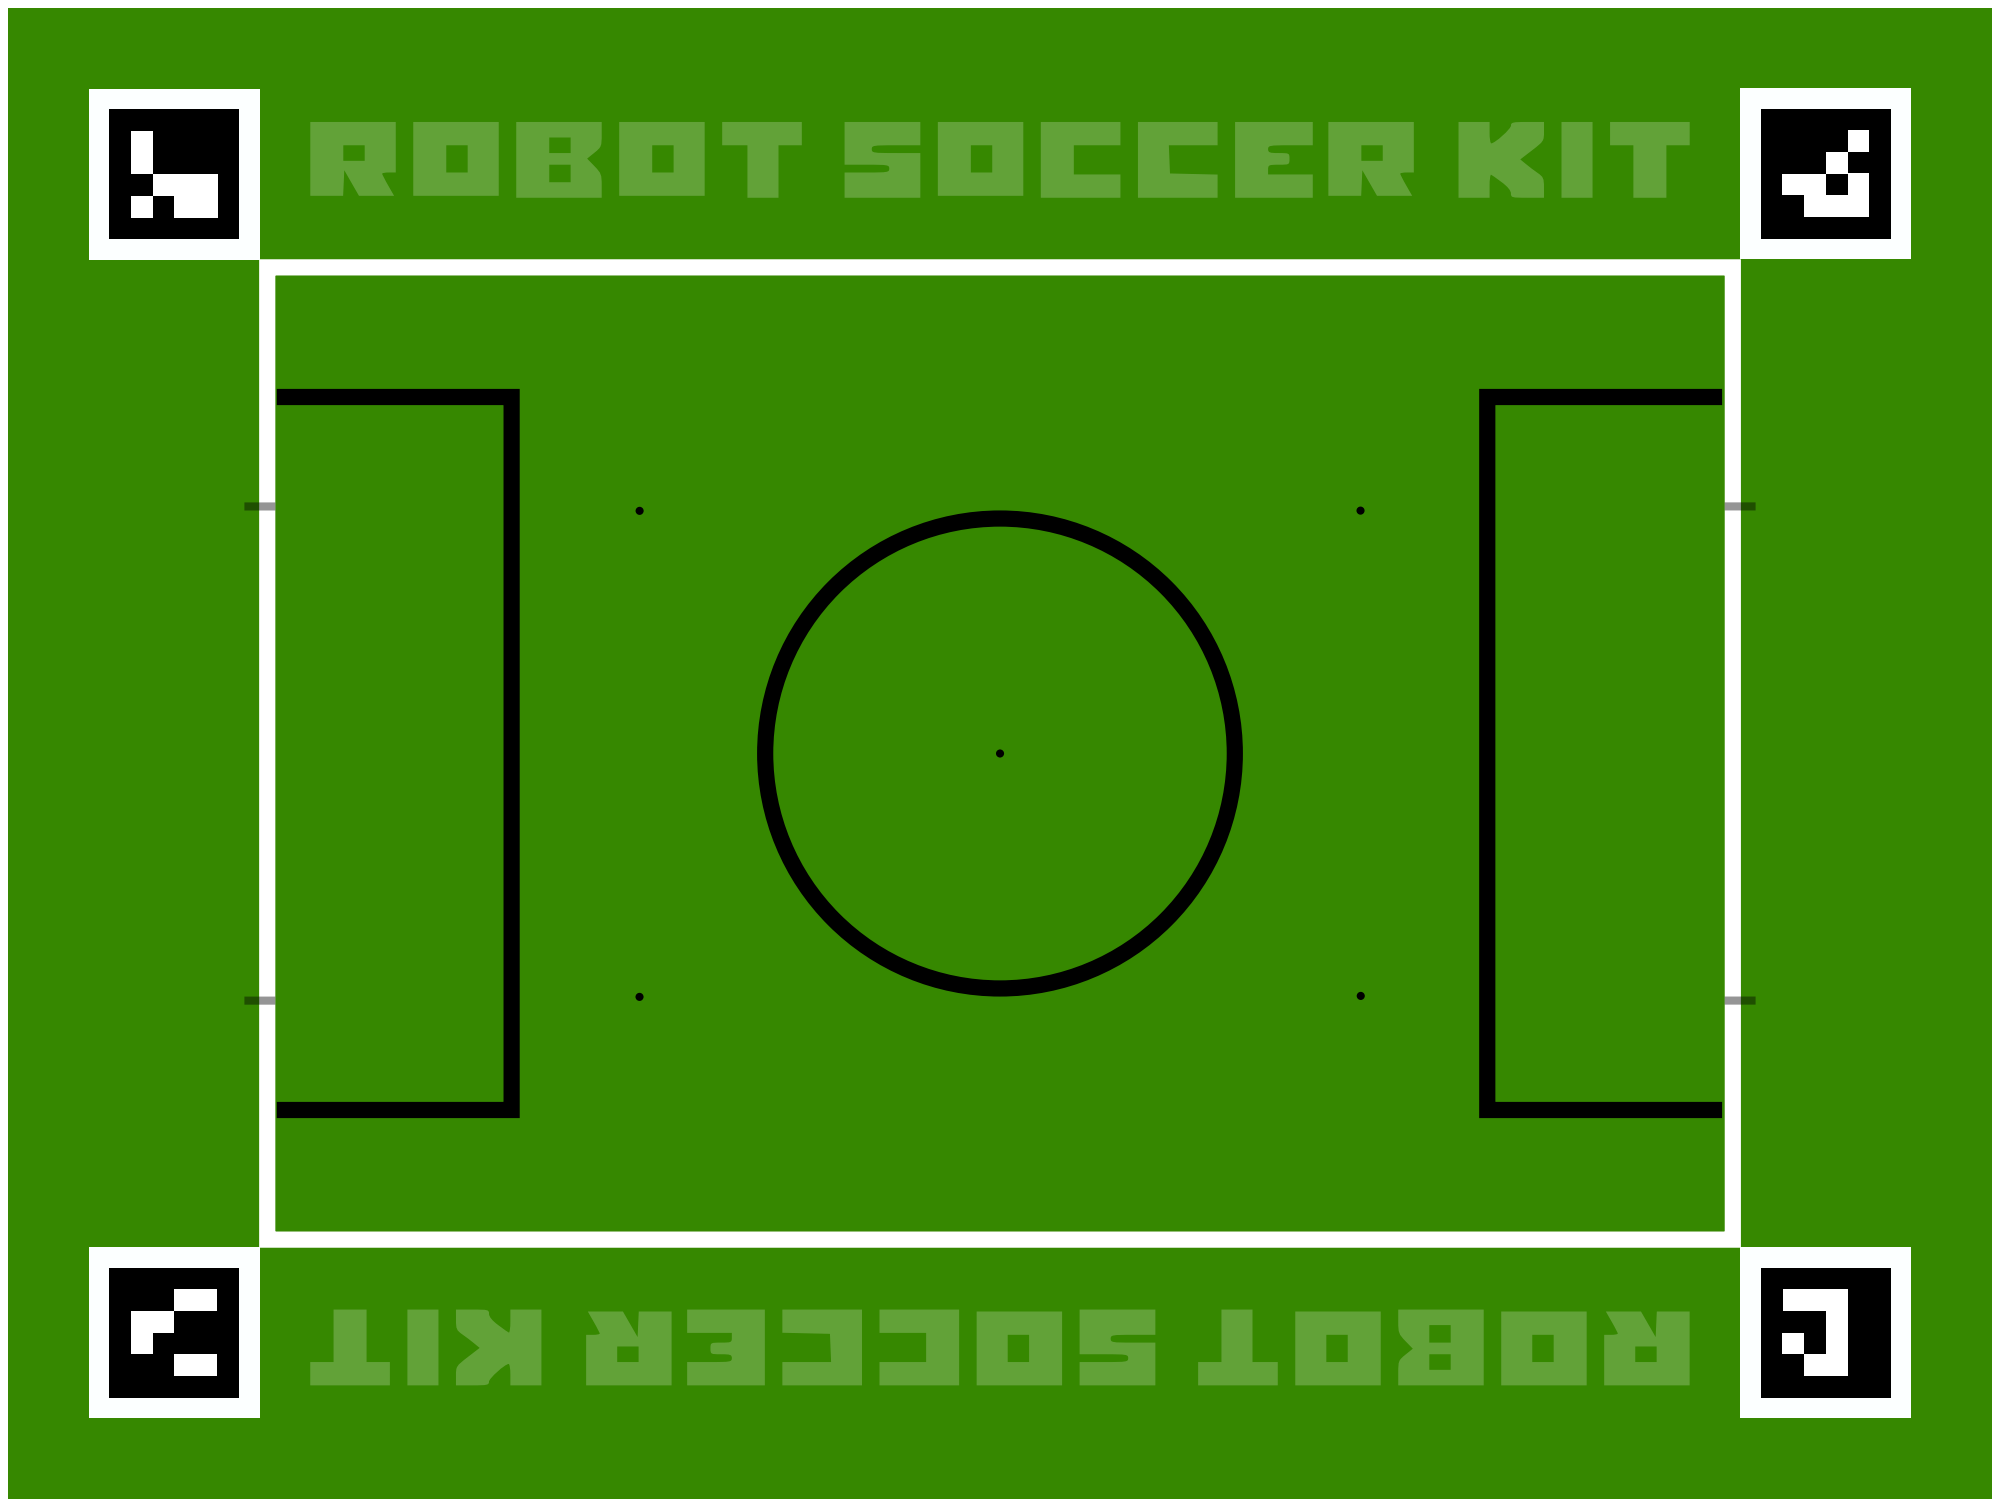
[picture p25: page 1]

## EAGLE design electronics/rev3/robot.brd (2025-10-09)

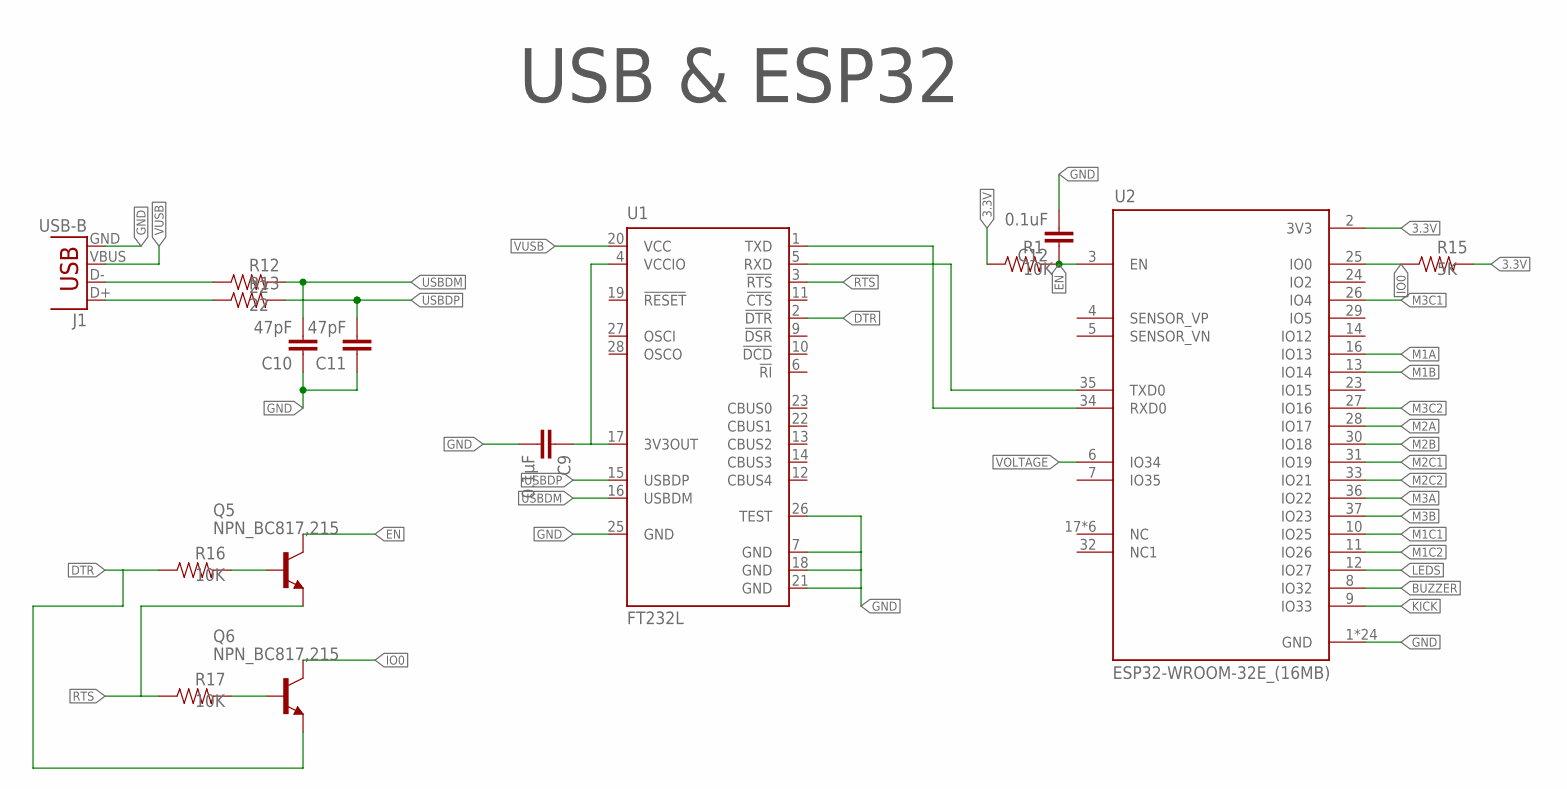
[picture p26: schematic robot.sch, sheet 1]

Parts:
C9: 0.1µF; 0805; FARNELL 2688486RL
C10, C11: 47pF; 0805; FARNELL 1081223
C12: 0.1uF; 0805; FARNELL 1081223
J1: USB-B; USB-B-PTH; FARNELL 1308876
Q5, Q6: NPN_BC817,215; SOT-23; FARNELL 1081223
R1, R16, R17: 10K; 0805; FARNELL 2446926
R12, R13: 22; 0805; FARNELL 2446926
R15: 5K; 0805; FARNELL 2446926
U1: FT232L; SSOP28; FARNELL 1146032
U2: ESP32-WROOM-32E_(16MB); MODULE_ESP32-WROOM-32E_(16MB); FARNELL ESP32-WROOM

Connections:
3.3V: R1.1, R15.2, U2.2 (3V3); also elsewhere on the board
BUZZER: U2.8 (IO32); also elsewhere on the board
DTR: Q6.2 (E), R16.1, U1.2 (!DTR)
EN: C12.1, Q5.3 (C), R1.2, U2.3 (EN)
GND: C9.2, C10.1, C11.1, C12.2, J1.GND, U1.7 (GND), U1.18 (GND), U1.21 (GND), U1.25 (GND), U1.26 (TEST), U2.1 (GND), U2.15 (GND), U2.38 (GND), U2.39_1 (GND), U2.39_2 (GND), U2.39_3 (GND), U2.39_4 (GND), U2.39_5 (GND), U2.39_6 (GND), U2.39_7 (GND), U2.39_8 (GND), U2.39_9 (GND), U2.39_10 (GND), U2.39_11 (GND), U2.39_12 (GND), U2.39_13 (GND), U2.39_14 (GND), U2.39_15 (GND), U2.39_16 (GND), U2.39_17 (GND), U2.39_18 (GND), U2.39_19 (GND), U2.39_20 (GND), U2.39_21 (GND); also elsewhere on the board
IO0: Q6.3 (C), R15.1, U2.25 (IO0)
KICK: U2.9 (IO33); also elsewhere on the board
LEDS: U2.12 (IO27); also elsewhere on the board
M1A: U2.16 (IO13); also elsewhere on the board
M1B: U2.13 (IO14); also elsewhere on the board
M1C1: U2.10 (IO25); also elsewhere on the board
M1C2: U2.11 (IO26); also elsewhere on the board
M2A: U2.28 (IO17); also elsewhere on the board
M2B: U2.30 (IO18); also elsewhere on the board
M2C1: U2.31 (IO19); also elsewhere on the board
M2C2: U2.33 (IO21); also elsewhere on the board
M3A: U2.36 (IO22); also elsewhere on the board
M3B: U2.37 (IO23); also elsewhere on the board
M3C1: U2.26 (IO4); also elsewhere on the board
M3C2: U2.27 (IO16); also elsewhere on the board
unnamed: U1.1 (TXD), U2.34 (RXD0)
unnamed: U1.5 (RXD), U2.35 (TXD0)
unnamed: C9.1, U1.4 (VCCIO), U1.17 (3V3OUT)
unnamed: Q5.1 (B), R16.2
unnamed: Q6.1 (B), R17.2
unnamed: J1.D-, R12.1
unnamed: J1.D+, R13.1
RTS: Q5.2 (E), R17.1, U1.3 (!RTS)
USBDM: C10.2, R12.2, U1.16 (USBDM)
USBDP: C11.2, R13.2, U1.15 (USBDP)
VOLTAGE: U2.6 (IO34); also elsewhere on the board
VUSB: J1.VBUS, U1.20 (VCC); also elsewhere on the board

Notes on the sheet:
USB & ESP32

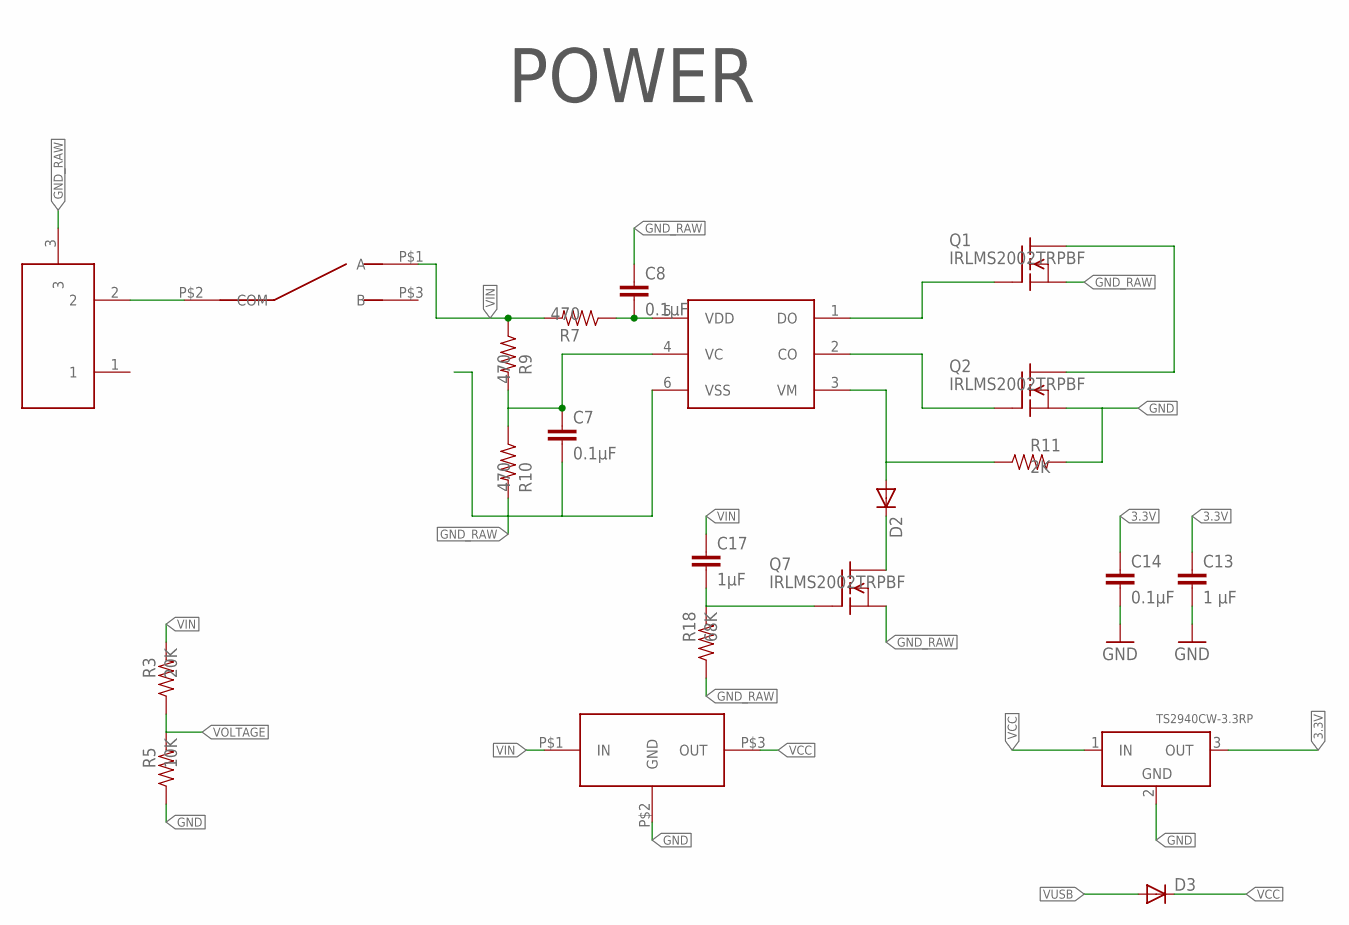
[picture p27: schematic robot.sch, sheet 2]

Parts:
C7, C8, C14: 0.1µF; 0805; FARNELL 2688486RL
C13: 1 µF; 0805; FARNELL 2688486RL
C17: 1µF; 0805; FARNELL 3010154
D2, D3: DIODESOD; SOD-323; FARNELL 8737843RL
J2: DC21MMX; DC-21MM; FARNELL 1217037
Q1, Q2, Q7: IRLMS2002TRPBF; SOT23-6; FARNELL 2577180RL
R3: 20K; 0805; FARNELL 2074395
R5: 10K; 0805; FARNELL 2074334RL
R7: 470; 0805; FARNELL 2447662
R9, R10: 470; 0805; FARNELL 2074334RL
R11: 2K; 0805; FARNELL 2447622
R18: 68K; 0805; FARNELL 2074486
REG1: REG_5V; TRACOPOWER; FARNELL 1696320
SW1: L102011ML04Q
U3: S8252; SOT23-6
U8: TS2940CW-3.3RP; SOT223; FARNELL 7261403

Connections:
1: J2.1
3.3V: C13.1, C14.1, U8.3 (OUT); also elsewhere on the board
GND: C13.2, C14.2, Q2.4 (S), R5.1, R11.2, REG1.P$2 (GND), U8.2 (GND); also elsewhere on the board
GND_RAW: C7.2, C8.1, J2.3, Q1.4 (S), Q7.4 (S), R10.2, R18.1, U3.6 (VSS)
unnamed: J2.2, SW1.P$2 (COM)
unnamed: C8.2, R7.1, U3.5 (VDD)
unnamed: C7.1, R9.2, R10.1, U3.4 (VC)
unnamed: Q1.1 (D), Q1.2 (D), Q1.5 (D), Q1.6 (D), Q2.1 (D), Q2.2 (D), Q2.5 (D), Q2.6 (D)
unnamed: Q2.3 (G), U3.2 (CO)
unnamed: Q1.3 (G), U3.1 (DO)
unnamed: D2.2 (A), R11.1, U3.3 (VM)
unnamed: C17.2, Q7.3 (G), R18.2
unnamed: D2.1 (C), Q7.1 (D), Q7.2 (D), Q7.5 (D), Q7.6 (D)
VCC: D3.1 (C), REG1.P$3 (OUT), U8.1 (IN); also elsewhere on the board
VIN: C17.1, R3.2, R7.2, R9.1, REG1.P$1 (IN), SW1.P$1 (A); also elsewhere on the board
VOLTAGE: R3.1, R5.2; also elsewhere on the board
VUSB: D3.2 (A); also elsewhere on the board

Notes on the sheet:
POWER

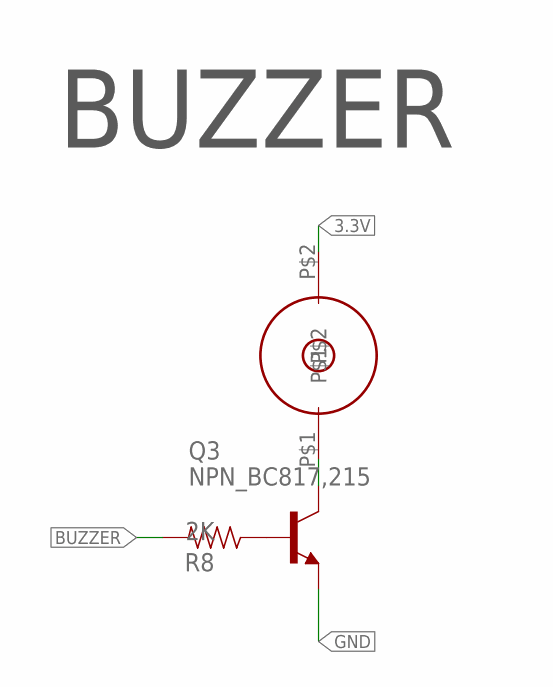
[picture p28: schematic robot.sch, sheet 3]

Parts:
B1: BUZZER66; FARNELL CEM-1203
Q3: NPN_BC817,215; SOT-23; FARNELL 1081223
R8: 2K; 0805; FARNELL 2447622

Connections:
3.3V: B1.P$2; also elsewhere on the board
BUZZER: R8.2; also elsewhere on the board
GND: Q3.2 (E); also elsewhere on the board
unnamed: Q3.1 (B), R8.1
unnamed: B1.P$1, Q3.3 (C)

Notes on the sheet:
BUZZER

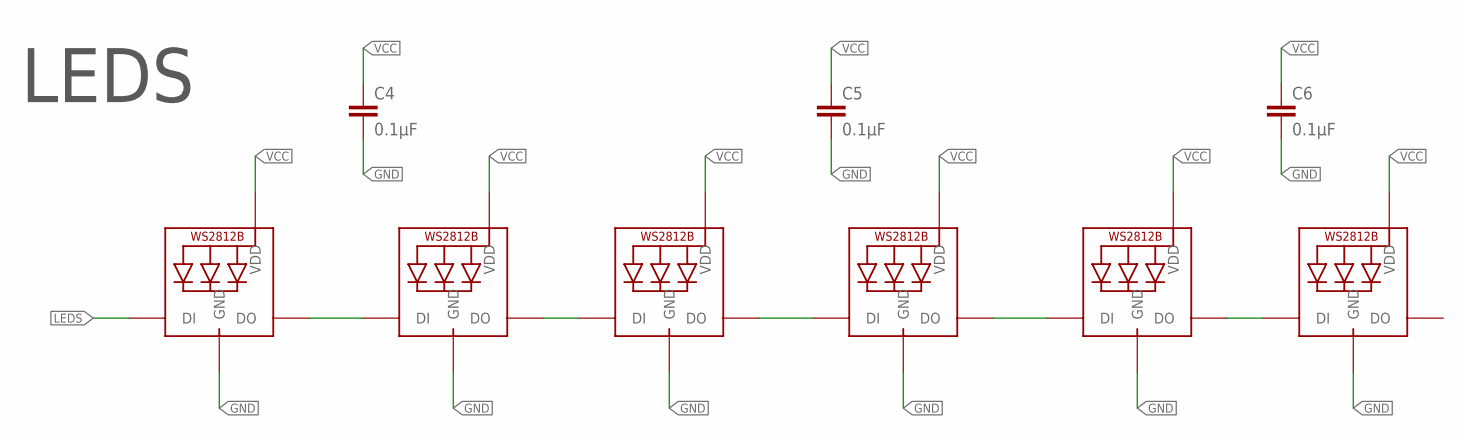
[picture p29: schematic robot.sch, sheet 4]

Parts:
C4, C5, C6: 0.1µF; 0805; FARNELL 2688486RL
LED1, LED2, LED3, LED4, LED5, LED6: WS2812B5050; WS2812B; FARNELL WS2812B 5050

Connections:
GND: C4.2, C5.2, C6.2, LED1.3-GND (GND), LED2.3-GND (GND), LED3.3-GND (GND), LED4.3-GND (GND), LED5.3-GND (GND), LED6.3-GND (GND); also elsewhere on the board
LEDS: LED1.4-DIN (DI); also elsewhere on the board
unnamed: LED1.2-DOUT (DO), LED2.4-DIN (DI)
unnamed: LED2.2-DOUT (DO), LED3.4-DIN (DI)
unnamed: LED4.2-DOUT (DO), LED5.4-DIN (DI)
unnamed: LED5.2-DOUT (DO), LED6.4-DIN (DI)
unnamed: LED3.2-DOUT (DO), LED4.4-DIN (DI)
VCC: C4.1, C5.1, C6.1, LED1.1-VDD (VDD), LED2.1-VDD (VDD), LED3.1-VDD (VDD), LED4.1-VDD (VDD), LED5.1-VDD (VDD), LED6.1-VDD (VDD); also elsewhere on the board

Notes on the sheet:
LEDS

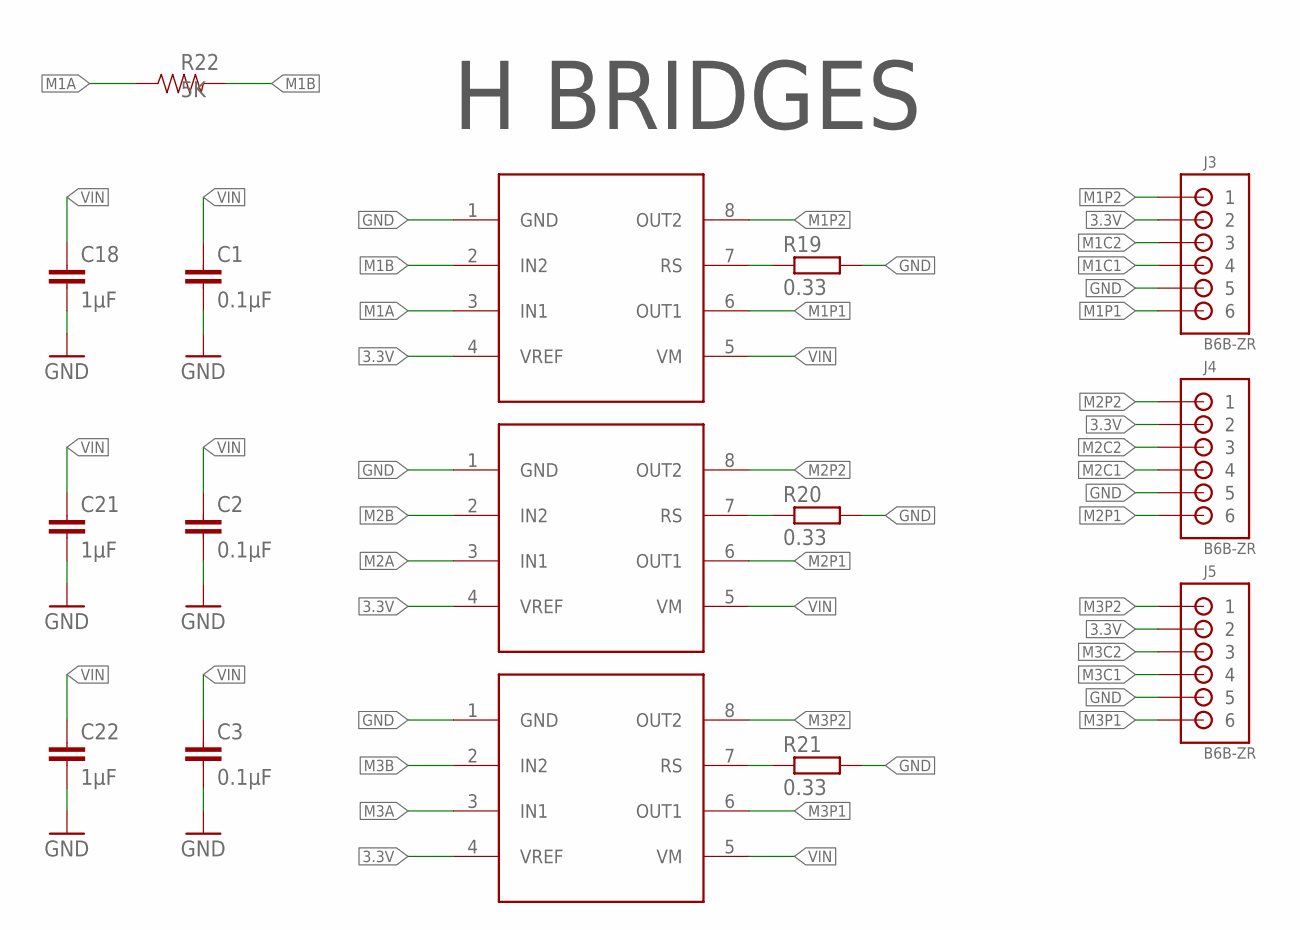
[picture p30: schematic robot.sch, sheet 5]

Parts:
C1, C2, C3: 0.1µF; 0805; FARNELL 2688486RL
C18, C21, C22: 1µF; 0805; FARNELL 2688486RL
J3, J4, J5: B6B-ZR; FARNELL 9491805
R19, R20, R21: 0.33; R1206
R22: 5K; 0805; FARNELL 2446926
U10, U11, U12: TB67H450FNG; HSOP8

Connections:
3.3V: J3.2, J4.2, J5.2, U10.4 (VREF), U11.4 (VREF), U12.4 (VREF); also elsewhere on the board
GND: C1.2, C2.2, C3.2, C18.2, C21.2, C22.2, J3.5, J4.5, J5.5, R19.2, R20.2, R21.2, U10.1 (GND), U11.1 (GND), U12.1 (GND); also elsewhere on the board
M1A: R22.1, U10.3 (IN1); also elsewhere on the board
M1B: R22.2, U10.2 (IN2); also elsewhere on the board
M1C1: J3.4; also elsewhere on the board
M1C2: J3.3; also elsewhere on the board
M1P1: J3.6, U10.6 (OUT1)
M1P2: J3.1, U10.8 (OUT2)
M2A: U11.3 (IN1); also elsewhere on the board
M2B: U11.2 (IN2); also elsewhere on the board
M2C1: J4.4; also elsewhere on the board
M2C2: J4.3; also elsewhere on the board
M2P1: J4.6, U11.6 (OUT1)
M2P2: J4.1, U11.8 (OUT2)
M3A: U12.3 (IN1); also elsewhere on the board
M3B: U12.2 (IN2); also elsewhere on the board
M3C1: J5.4; also elsewhere on the board
M3C2: J5.3; also elsewhere on the board
M3P1: J5.6, U12.6 (OUT1)
M3P2: J5.1, U12.8 (OUT2)
unnamed: R19.1, U10.7 (RS)
unnamed: R20.1, U11.7 (RS)
unnamed: R21.1, U12.7 (RS)
VIN: C1.1, C2.1, C3.1, C18.1, C21.1, C22.1, U10.5 (VM), U11.5 (VM), U12.5 (VM); also elsewhere on the board

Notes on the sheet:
H BRIDGES

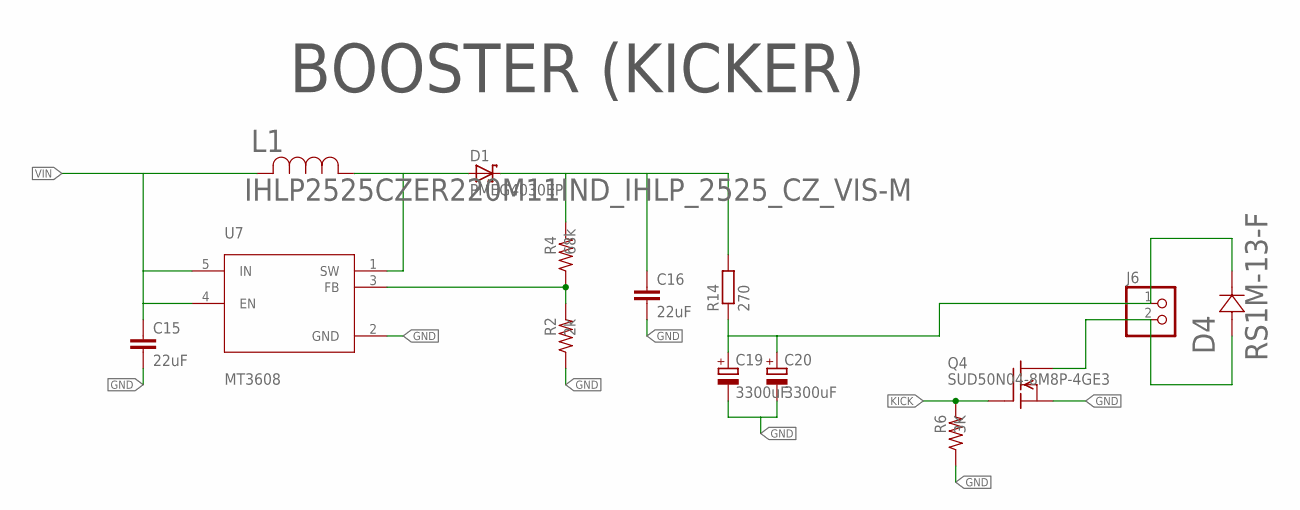
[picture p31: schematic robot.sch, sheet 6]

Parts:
C15, C16: 22uF; C0805; FARNELL 2666560
C19, C20: 3300uF; E5-13; MOUSER 710-860160278042
D1: PMEG4030EP; SOD128; FARNELL 1829201
D4: RS1M-13-F; RS1M
J6: RHOBAN_KICKER; FARNELL JF-0530B
L1: IHLP2525CZER220M11IND_IHLP_2525_CZ_VIS-M; IND_IHLP_2525_CZ_VIS-M; FARNELL 1741369
Q4: SUD50N04-8M8P-4GE3; TO252; FARNELL 1794799
R2: 2k; 0805; FARNELL 2447622
R4: 68k; 0805; FARNELL 2447023
R6: 3K; 0805; FARNELL 1887603
R14: 270; R2010; FARNELL 1887603
U7: MT3608; SOT95P280X145-6N; FARNELL MT3608

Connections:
GND: C15.2, C16.2, C19.-, C20.-, Q4.2 (S), R2.1, R6.1, U7.2 (GND); also elsewhere on the board
KICK: Q4.1 (G), R6.2; also elsewhere on the board
KICKER: D4.A, J6.2, Q4.3 (D)
unnamed: D1.2 (A), L1.1, U7.1 (SW)
unnamed: C16.1, D1.1 (K), R4.2, R14.2
unnamed: R2.2, R4.1, U7.3 (FB)
VIN: C15.1, L1.2, U7.4 (EN), U7.5 (IN); also elsewhere on the board
VSTORE: C19.+, C20.+, D4.K, J6.1, R14.1

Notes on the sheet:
BOOSTER (KICKER)

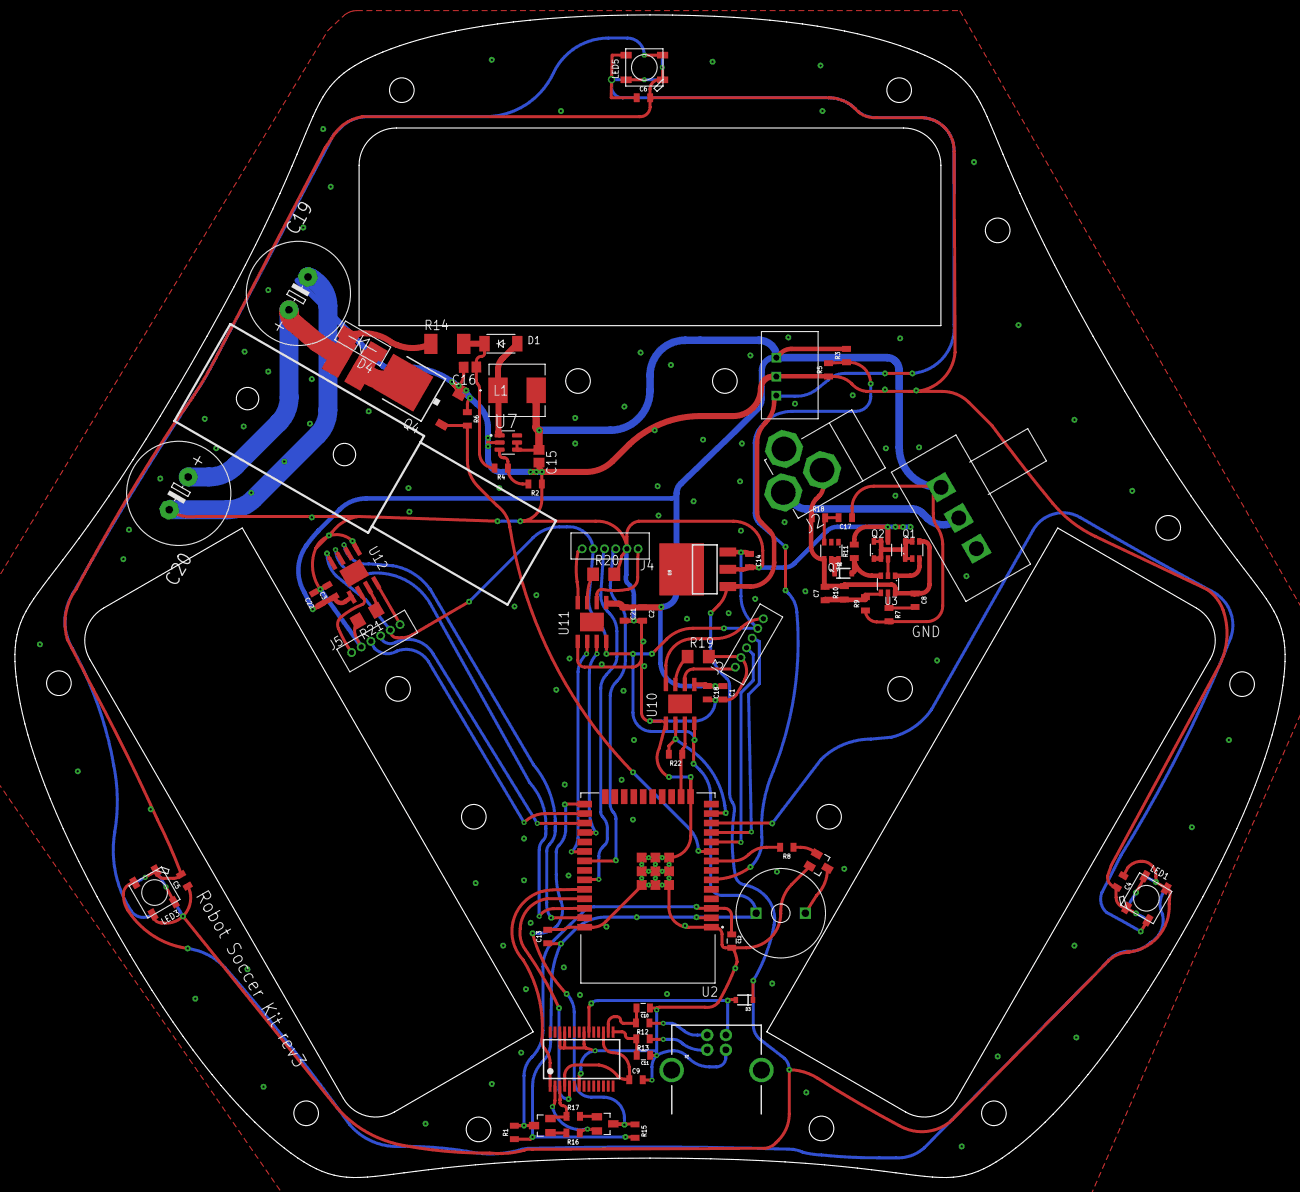
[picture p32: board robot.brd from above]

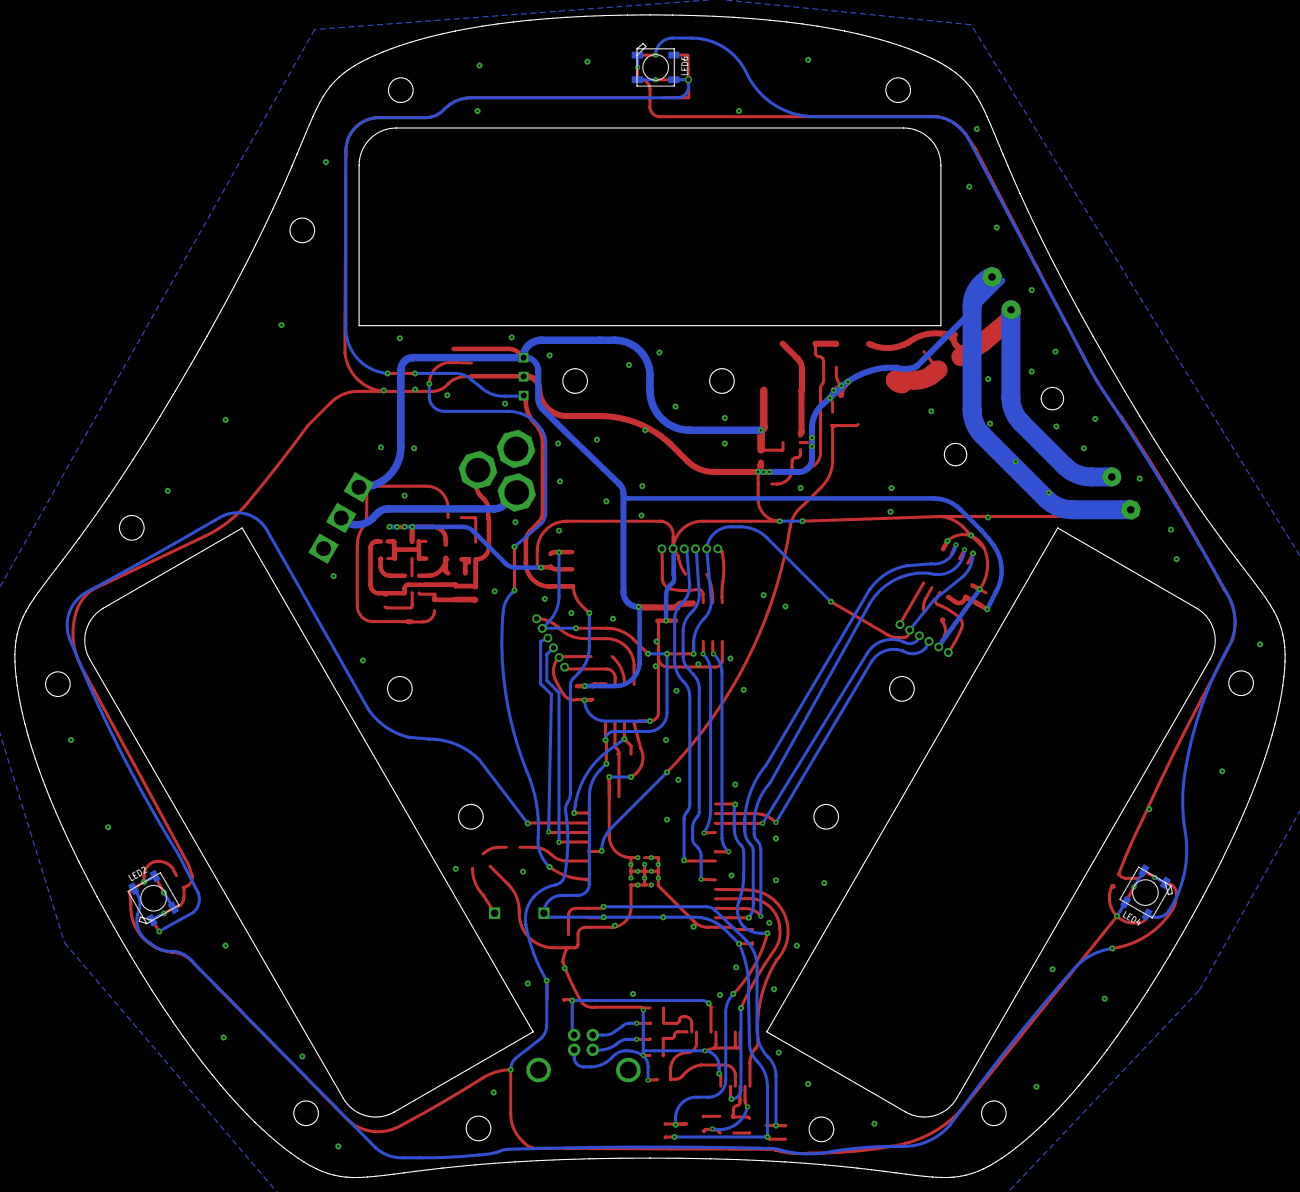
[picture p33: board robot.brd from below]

Board: 2 copper layers, 170.3 x 155.9 mm, 95 parts (3 on the bottom side), 65 nets.

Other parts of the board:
U$2, U$3, U$4, U$5, U$6, U$8, U$9, U$10, U$11, U$15, U$31, U$33, U$35, U$36, U$38, U$39: STAND-OFF

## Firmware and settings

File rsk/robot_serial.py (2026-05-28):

import numpy as np
import threading
import time
import serial
from serial.tools import list_ports
import logging
from . import robot
from .packets import (
    Packet,
    PacketReader,
    PACKET_ROBOT,
    PACKET_ROBOT_CONTROL,
    PACKET_ROBOT_BEEP,
    PACKET_ROBOT_LEDS_CUSTOM,
    PACKET_ROBOT_KICK,
    PACKET_MONITOR_DATA,
    PACKET_MONITOR,
)
from .robots import Robots

logger: logging.Logger = logging.getLogger("robot")


class RobotSerial(robot.Robot):
    """
    Connection with a physical robot
    """

    def __init__(self, robots: Robots, url: str):
        super().__init__(robots, url)

        # Instance of serial connection
        self.bt = None
        # Is the connection initialized ?
        self.init: bool = True
        # Is the thread running ?
        self.running: bool = True
        # Last message timestamps
        self.last_sent_message = None
        # Last initialization tinestamp
        self.last_init = None
        # State retrieved from the packets
        self.state = {}

        # Starting the threads
        self.thread = threading.Thread(
            target=lambda: self.run_thread(), daemon=True, name="RobotSerialThread"
        )
        self.thread.start()

        # Pending packets queued
        self.pending_packets = {}
        self.lock = threading.Lock()

    def available_urls() -> list:
        return [entry.device for entry in list_ports.comports()]

    def monitor(self, frequency: int) -> None:
        """
        Send a monitor command to the robot

        :param int frequency: monitor frequency (Hz)
        """
        packet = Packet(PACKET_MONITOR)
        packet.append_int(frequency)
        self.add_packet("monitor", packet)

    def blink(self) -> None:
        """
        Gets the robot blinking for a while
        """
        for _ in range(5):
            self.leds(255, 255, 255)
            time.sleep(0.25)
            self.leds(0, 0, 0)
            time.sleep(0.25)
        self.leds_dirty = True

    def process(self, packet: Packet) -> None:
        """
        Processes a packet

        :param Packet packet: packet to process
        """
        if packet.type == PACKET_MONITOR_DATA:
            self.last_message = time.time()
            state = {}
            version = packet.readByte()
            state["version"] = version

            if version == 11:
                # Version 11, old robots
                state["time"] = packet.read_float()
                state["distance"] = packet.read_small_float()
                state["optics"] = [packet.readByte() for optic in range(7)]
                state["wheels"] = [packet.read_small_float() for w in range(3)]
                state["yaw"] = packet.read_small_float()
                state["gyro_yaw"] = packet.read_small_float()
                state["pitch"] = packet.read_small_float()
                state["roll"] = packet.read_small_float()
                state["odometry"] = {
                    "x": packet.read_short() / 1000.0,
                    "y": packet.read_short() / 1000.0,
                    "yaw": packet.read_small_float(),
                }
                state["battery"] = [packet.readByte() / 40.0, packet.readByte() / 40.0]

            elif version == 2:
                # Version 2, new robots
                state["time"] = packet.read_float()
                state["battery"] = [packet.readByte() / 10.0]
            else:
                logger.error(f"Unknown firmware version {version}")
            self.state = state

    def add_packet(self, name: str, packet: Packet) -> None:
        """
        Adds a packet to the pending packets

        :param str name: the name of the packet, if such a name is in used, it will be overwritten
        :param Packet packet: packet to send
        """
        self.lock.acquire()
        self.pending_packets[name] = packet
        self.lock.release()

    def pop_packet(self):
        """
        Gets the next pending packet to be sent if any

        :return Packet|None: a packet, or None
        """
        packet = None

        self.lock.acquire()
        if len(self.pending_packets) > 0:
            name = next(iter(self.pending_packets))
            packet = self.pending_packets[name]
            del self.pending_packets[name]
        self.lock.release()

        return packet

    def beep(self, frequency: int, duration: int):
        """
        Gets the robot beeping

        :param int frequency: frequency (Hz)
        :param int duration: duration (ms)
        """
        packet = Packet(PACKET_ROBOT)
        packet.append_byte(PACKET_ROBOT_BEEP)
        packet.append_short(frequency)
        packet.append_short(duration)
        self.add_packet("beep", packet)

    def kick(self, power: float = 1.0):
        """
        Gets the robot kicking

        :param float power: kick intensity (0 to 1), defaults to 1.
        """
        packet = Packet(PACKET_ROBOT)
        packet.append_byte(PACKET_ROBOT_KICK)
        packet.append_byte(int(100 * power))
        self.add_packet("kick", packet)

    def control(self, dx: float, dy: float, dturn: float):
        """
        Sends some chassis speed order fo the robot

        :param float dx: x speed (m/s)
        :param float dy: y speed (m/s)
        :param float dturn: rotational speed (rad/s)
        """
        packet = Packet(PACKET_ROBOT)
        packet.append_byte(PACKET_ROBOT_CONTROL)
        packet.append_short(int(1000 * dx))
        packet.append_short(int(1000 * dy))
        packet.append_short(int(np.rad2deg(dturn)))
        self.add_packet("control", packet)

    def leds(self, red: int, green: int, blue: int) -> None:
        """
        Sets the robot LEDs

        :param int r: R intensity (0-255)
        :param int g: G intensity (0-255)
        :param int b: B intensity (0-255)
        """
        super().leds(red, green, blue)

        packet = Packet(PACKET_ROBOT)
        packet.append_byte(PACKET_ROBOT_LEDS_CUSTOM)
        packet.append_byte(red)
        packet.append_byte(green)
        packet.append_byte(blue)
        self.add_packet("leds", packet)

    def stop(self):
        """
        Stops the robot from moving
        """
        self.control(0, 0, 0)

    def close(self):
        """
        Stops the robot's thread
        """
        self.running = False

    def run_thread(self):
        """
        Process the main thread
        """
        packet_reader = PacketReader()

        while self.running:
            try:
                if self.init:
                    logger.info(f"Opening connection with {self.url}")
                    self.init = False
                    if self.bt is not None:
                        self.bt.close()
                        self.bt = None
                    self.bt = serial.Serial(self.url, timeout=0.02)
                    time.sleep(0.1)
                    self.bt.write(b"rhock\r\nrhock\r\nrhock\r\n")
                    time.sleep(0.1)
                    self.monitor(5)
                    self.control(0, 0, 0)
                    self.beep(880, 250)
                    packet_reader.reset()
                    self.last_init = time.time()
                    self.last_sent_message = None

                # Receiving data
                byte = self.bt.read(1)
                if len(byte):
                    packet_reader.push(ord(byte))
                    if packet_reader.has_packet():
                        self.process(packet_reader.pop_packet())

                # Asking periodically for robot monitor status
                if (
                    self.last_sent_message is None
                    or time.time() - self.last_sent_message > 1.0
                ):
                    self.monitor(1)

                # Sending pending packets
                packet = self.pop_packet()
                while packet is not None:
                    self.last_sent_message = time.time()
                    if self.bt is not None and self.bt.is_open:
                        self.bt.write(packet.to_raw())
                    packet = self.pop_packet()

            except (OSError, serial.serialutil.SerialException) as e:
                # In case of exception, we re-init the connection
                logger.error(f"Error: {e}")

                if "FileNotFoundError" in str(e):
                    time.sleep(1.0)

                self.init = True

            # If we didn't receive a message for more than 5s, we re-init the connection
            no_message = (self.last_message is None) or (
                time.time() - self.last_message > 5
            )

            if self.last_init is None:
                old_init = False
            else:
                old_init = time.time() - self.last_init > 5

            if no_message and old_init:
                self.init = True

        if self.bt is not None:
            self.bt.close()


if __name__ == "__main__":
    r = RobotSerial("/dev/rfcomm0")

    while True:
        print(r.state)
        time.sleep(5)

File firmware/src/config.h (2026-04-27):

#pragma once

#define WIFI_SSID "RSK_Field_WiFi"
#define WIFI_PASSWORD "RSK_FIELD_PASSWORD"

#define WIFI_IP "192.168.100.101"
#define WIFI_SUBNET "255.255.255.0"
#define WIFI_GATEWAY "192.168.100.254"
#define WIFI_DNS WIFI_GATEWAY

#define WIFI_UDP_PORT 7600

// Robot's name when in Bluetooth mode
#define ROBOT_NAME "RSK"
// #define FORCE_BLUETOOTH

#define KICK_PIN 33

// Wheels gear reduction ratio
#define REDUCTION_RATIO 100

// Cycles per revolution [cycles/turn]
// The minus sign is here because encoder increments in reverted order with
// respect to pwm
#define WHEELS_CPR (7 * 4 * REDUCTION_RATIO)

// Window size for speed estimation (since we are servoing at 1Khz; this can be
// considered as the amount of milliseconds used for finite differences speed
// estimation)
#define SPEED_WINDOW 5

// Does the motors (positive) rotation gets the robot rotating positively (counter-clockwise)?
#define MOTORS_ROTATION_SIGN 1

// Board revision
#define BOARD_REV2

// Wheels orientations [deg]
// In chassis frame, the front axis is the x axis running through the kicker of
// the robot Those are orientation of the driving direction of the wheels,
// assuming they rotate in the direction that makes the robot rotate p=ositively
#ifdef BOARD_REV2
#define WHEEL1_ALPHA -90
#define WHEEL2_ALPHA 30
#define WHEEL3_ALPHA 150
#else
#define WHEEL1_ALPHA 150
#define WHEEL2_ALPHA -90
#define WHEEL3_ALPHA 30
#endif

// This define uses BRAKE mode to drive the motors
// #ifdef BOARD_REV2
// #define MOTORS_BRAKE
// #endif

// Wheel radius [m]
#define MODEL_WHEEL_RADIUS 0.035

// Distance from robot center to wheel [m]
#define MODEL_ROBOT_RADIUS 0.0595

// Maximum wheels speed [rad/s]
#define MAX_WHEEL_SPEEDS 16

// Motors wiring pins (PWM for the two directions and A/B encoders)
#ifdef BOARD_REV2
#define MOTOR1_PWM1 13
#define MOTOR1_PWM2 14
#define MOTOR1_ENC1 25
#define MOTOR1_ENC2 26

#define MOTOR2_PWM1 17
#define MOTOR2_PWM2 18
#define MOTOR2_ENC1 19
#define MOTOR2_ENC2 21

#define MOTOR3_PWM1 22
#define MOTOR3_PWM2 23
#define MOTOR3_ENC1 4
#define MOTOR3_ENC2 16
#else
#define MOTOR1_PWM1 13
#define MOTOR1_PWM2 14
#define MOTOR1_ENC1 4
#define MOTOR1_ENC2 16

#define MOTOR2_PWM1 17
#define MOTOR2_PWM2 18
#define MOTOR2_ENC1 19
#define MOTOR2_ENC2 21

#define MOTOR3_PWM1 22
#define MOTOR3_PWM2 23
#define MOTOR3_ENC1 25
#define MOTOR3_ENC2 26
#endif

// LEDs pin (6 RGB addressable WS2812 LEDs)
#define LEDS 27

// Buzzer pin
#define BUZZER 32

// Input voltage sampling pin
#define VOLTAGE 34

// Voltage divider resistors (Kohms)
#define VOLTAGE_R1 20
#define VOLTAGE_R2 10

// Maximum kick duration (microseconds)
#define KICK_MAX_DURATION 20000

// Below this voltage, the robot won't start moving, between USB voltage (see
// below) and this voltage, the robot will enter alarm mode
#define VOLTAGE_MIN 6.4

// Below this voltage, the robot is considered operated with USB
#define VOLTAGE_USB 5.0

// Set to disable WiFi power saving mode (which can cause latency issues)
// #define DISABLE_WIFI_POWER_SAVING

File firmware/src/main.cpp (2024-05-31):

#include "alert.h"
#include "com.h"
#include "buzzer.h"
#include "kicker.h"
#include "leds.h"
#include "motors.h"
#include "voltage.h"
#include <WiFi.h>
#include <WiFiUdp.h>

void setup() {

  leds_init();
  kicker_init();
  motors_init();
  buzzer_init();
  voltage_init();
  com_init();
  buzzer_play(MELODY_BOOT);
}

void loop() {
  buzzer_tick();
  kicker_tick();
  voltage_tick();
  alert_tick();
  com_tick();
  
}

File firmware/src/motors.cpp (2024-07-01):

#include "motors.h"
#include "buzzer.h"
#include "config.h"
#include "pwm_channels.h"
#include "shell.h"
#include "utils.h"
#include "voltage.h"
#include <Arduino.h>
#include <ESP32Encoder.h>
#include <Ticker.h>
#include <math.h>

Ticker servoTicker;

struct Motor {
  // Pins for PWM control
  int pin_pwm1;
  int pin_pwm2;
  // Pins for encoders
  int pin_enc1;
  int pin_enc2;
  // Wheel driving vector
  float drive_x;
  float drive_y;

  // PWM Channels used for pwm control
  int pwm_chan1;
  int pwm_chan2;
  // Encoder
  ESP32Encoder encoder;
  int64_t encoder_window[SPEED_WINDOW];
  uint32_t encoder_window_index;
  // Current target and measured speed
  float speed_target;
  float speed;
  // Current error
  float error;
  // Error accumulator (for integrator)
  float error_accumulator;
  // Is the servoing enabled ?
  bool enabled;
};

SHELL_PARAMETER_FLOAT(kp, "Kp", 1000);
SHELL_PARAMETER_FLOAT(ki, "Ki", 500);

#define DEG2RAD(x) (x * M_PI / 180.0)

struct Motor motors[] = {
    {MOTOR1_PWM1, MOTOR1_PWM2, MOTOR1_ENC1, MOTOR1_ENC2,
     (float)cos(DEG2RAD(WHEEL1_ALPHA)), (float)sin(DEG2RAD(WHEEL1_ALPHA))},
    {MOTOR2_PWM1, MOTOR2_PWM2, MOTOR2_ENC1, MOTOR2_ENC2,
     (float)cos(DEG2RAD(WHEEL2_ALPHA)), (float)sin(DEG2RAD(WHEEL2_ALPHA))},
    {MOTOR3_PWM1, MOTOR3_PWM2, MOTOR3_ENC1, MOTOR3_ENC2,
     (float)cos(DEG2RAD(WHEEL3_ALPHA)), (float)sin(DEG2RAD(WHEEL3_ALPHA))},
};

SHELL_PARAMETER_INT(n, "Counting", 0);

void _bound_pwm(float *value) {
  if (*value < -1024) {
    *value = -1024;
  }
  if (*value > 1024) {
    *value = 1024;
  }
}

int64_t motors_get_encoder(int index) {
  return motors[index].encoder.getCount();
}

bool motors_are_enabled() {
  return motors[0].enabled || motors[1].enabled || motors[2].enabled;
}

void motors_servo() {
  for (int k = 0; k < 3; k++) {
    int64_t count = motors[k].encoder.getCount();
    motors[k].encoder_window_index += 1;
    if (motors[k].encoder_window_index >= SPEED_WINDOW) {
      motors[k].encoder_window_index = 0;
    }

    int64_t delta =
        count - motors[k].encoder_window[motors[k].encoder_window_index];
    motors[k].encoder_window[motors[k].encoder_window_index] = count;

    motors[k].speed =
        (delta * 2 * M_PI * 1000.0) / ((float)(SPEED_WINDOW * WHEELS_CPR));
    float error = motors[k].speed_target - motors[k].speed;
    motors[k].error = error;

    if (motors[k].enabled) {
      motors[k].error_accumulator += ki * error / 1000.0;
      _bound_pwm(&motors[k].error_accumulator);

      float pwm = kp * error + motors[k].error_accumulator;
      _bound_pwm(&pwm);

      if (fabs(motors[k].speed_target) < 1e-3) {
        pwm = 0.0;
      }

      motors_set_pwm(k, pwm);
    } else {
      motors[k].error_accumulator = 0;
    }
  }
  n += 1;
}

void motors_init() {
  int pwm_channel;
  for (int k = 0; k < 3; k++) {
    pwm_channel = pwm_channel_allocate();
    ledcSetup(pwm_channel, 22000, 10);
    ledcAttachPin(motors[k].pin_pwm1, pwm_channel);
    motors[k].pwm_chan1 = pwm_channel;

    pwm_channel = pwm_channel_allocate();
    ledcSetup(pwm_channel, 22000, 10);
    motors[k].pwm_chan2 = pwm_channel;
    ledcAttachPin(motors[k].pin_pwm2, pwm_channel);

    motors[k].encoder.attachFullQuad(motors[k].pin_enc1, motors[k].pin_enc2);
    for (int i = 0; i < SPEED_WINDOW; i++) {
      motors[k].encoder_window[i] = 0;
    }
    motors[k].encoder_window_index = 0;
    motors[k].speed = 0;
    motors[k].error = 0;
    motors[k].speed_target = 0;
    motors[k].error_accumulator = 0;
    motors[k].enabled = false;
  }

  // Configuring a 1000 Hz timer
  servoTicker.attach_ms(1, motors_servo);
}

void motors_set_pwm(int index, int16_t pwm) {
  if (voltage_can_move() || pwm == 0) {
    if (index >= 0 && index < 3) {
      if (pwm < -1024)
        pwm = -1024;
      if (pwm > 1024)
        pwm = 1024;

      if (pwm > 0) {
#ifdef MOTORS_BRAKE
        ledcWrite(motors[index].pwm_chan1, 1024 - pwm);
        ledcWrite(motors[index].pwm_chan2, 1024);
#else
        ledcWrite(motors[index].pwm_chan1, 0);
        ledcWrite(motors[index].pwm_chan2, pwm);
#endif
      } else {
        pwm = -pwm;
#ifdef MOTORS_BRAKE
        ledcWrite(motors[index].pwm_chan1, 1024);
        ledcWrite(motors[index].pwm_chan2, 1024 - pwm);
#else
        ledcWrite(motors[index].pwm_chan1, pwm);
        ledcWrite(motors[index].pwm_chan2, 0);
#endif
      }
    }
  } else {
    buzzer_play(MELODY_WARNING);
    motors_disable();
  }
}

void motors_set_pwms(int16_t motor1, int16_t motor2, int16_t motor3) {
  motors_set_pwm(0, motor1);
  motors_set_pwm(1, motor2);
  motors_set_pwm(2, motor3);
}

void motors_set_speed(int index, float speed) {
  motors[index].speed_target = speed;
  motors[index].enabled = true;
}

void motors_set_speeds(float w1, float w2, float w3) {
  motors_set_speed(0, w1);
  motors_set_speed(1, w2);
  motors_set_speed(2, w3);
}

void motors_set_ik(float dx, float dy, float dt) {
  float w1 = MOTORS_ROTATION_SIGN *
             (motors[0].drive_x * dx + motors[0].drive_y * dy +
              MODEL_ROBOT_RADIUS * dt) /
             (MODEL_WHEEL_RADIUS);
  float w2 = MOTORS_ROTATION_SIGN *
             (motors[1].drive_x * dx + motors[1].drive_y * dy +
              MODEL_ROBOT_RADIUS * dt) /
             (MODEL_WHEEL_RADIUS);
  float w3 = MOTORS_ROTATION_SIGN *
             (motors[2].drive_x * dx + motors[2].drive_y * dy +
              MODEL_ROBOT_RADIUS * dt) /
             (MODEL_WHEEL_RADIUS);

  float max_speed = fmax(fmax(fabs(w1), fabs(w2)), fabs(w3));
  if (max_speed > MAX_WHEEL_SPEEDS) {
    float ratio = MAX_WHEEL_SPEEDS / max_speed;
    w1 *= ratio;
    w2 *= ratio;
    w3 *= ratio;
  }

  motors_set_speeds(w1, w2, w3);
}

SHELL_COMMAND(motors, "Motors status") {
  for (int k = 0; k < 3; k++) {
    shell_stream()->print("Motor #");
    shell_stream()->print((int)k);
    shell_stream()->println(": ");

    shell_stream()->print("- Encoder (pulses): ");
    shell_stream()->println((int)motors[k].encoder.getCount());
    shell_stream()->print("- Speed (rad/s): ");
    shell_stream()->println(motors[k].speed);
    shell_stream()->print("- Error: ");
    shell_stream()->println(motors[k].error);
    shell_stream()->print("- Error accumulator: ");
    shell_stream()->println(motors[k].error_accumulator);
  }
}

SHELL_COMMAND(pwms, "Test motor (set pwms)") {
  if (argc > 2) {
    motors_set_pwms(atoi(argv[0]), atoi(argv[1]), atoi(argv[2]));
  } else {
    shell_stream()->println("Usage: pwms [pwm1] [pwm2] [pwm3]");
  }
}

SHELL_COMMAND(servo, "Servo targets") {
  if (argc > 2) {
    motors_set_speeds(atof_nonan(argv[0]), atof_nonan(argv[1]),
                      atof_nonan(argv[2]));
  } else {
    shell_stream()->println("Usage: servo [speed1] [speed2] [speed3]");
  }
}

SHELL_COMMAND(ik, "Servo chassis speed") {
  if (argc > 2) {
    motors_set_ik(atof_nonan(argv[0]), atof_nonan(argv[1]),
                  atof_nonan(argv[2]));
  } else {
    shell_stream()->println("Usage: ik [dx] [dy] [dt]");
  }
}
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

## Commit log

2021-09-02 Adding saturation (fixes #4)
    [backend.py, detection.py, robots.py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]
2021-09-03 DXF marker part
    [marker.dxf]
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2021-09-07 Field calibration is now undone when corners are misprojected
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2021-09-13 Fixes in client to stop properly
    [client.py]
2021-09-13 More accurate error when robot is not known
    [control.py]
2021-09-13 Moving to app/
    [marker.dxf]
2021-09-13 Renaming app to ssl
    [marker.dxf]
2021-09-20 Fixing ball filter and publish
    [detection.py]
2021-09-21 Fixing None ball, aesthetic
    [client.py, detection.py]
2021-09-24 Moving PDFs and SVGs
    [marker.dxf]
2021-09-24 Committing electronics and firmware
    [BOM.xlsx, holo.brd, holo.sch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]
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2021-10-05 Switching to new camera
2021-10-08 Fixing unit in Identify
    [robots.py]
2021-10-08 Documenting markers, referencing a camera
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2021-10-24 Fixing BOM
    [BOM.xlsx]
2021-10-26 Fixed typo
    [ball.csv, log.csv]
2021-10-27 Removing csvs
    [ball.csv, log.csv]
2021-10-28 Dealing with packets asynchronously with control thread, handling more errors
    [client.py, detection.py, robot.py]
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2021-12-08 Avoiding spamming when COM doesn't exists
    [robot.py]
2021-12-08 Masking SIGINT during client thread lock
2021-12-08 Less brightness on LEDs
2021-12-09 Detecting on annotated images (temp fix)
    [video.py]
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2022-01-11 Switching from red to green
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2022-01-11 Only publishing calibrated balls
2022-01-11 Switching to waitress for serving
2022-01-11 Retrieving errors in client API
    [game_controller.py]
2022-01-11 Restarting BT in mount.sh
2022-01-11 Enhancing UI (fixes #18 / fixes #11)
    [detection.py, field.py]
2022-01-14 Copying driver files from script dir
2022-01-26 Removing all components that will be replaced
    [holo.brd, holo.sch]
2022-01-28 Rework done
    [holo.brd, holo.sch]
2022-01-28 Removing former directories (electronics merged)
    [BOM.xlsx, holo.brd, holo.sch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]
2022-01-28 Autorouting to test
    [robot.brd, robot.sch]
2022-01-28 BMS resistors
    [robot.brd, robot.sch]
2022-01-29 DTR/RTS ESP programming and fixes
    [robot.brd, robot.sch]
2022-01-31 Minor fixes
    [robot.brd, robot.sch]
2022-01-31 rev0 new board
    [robot.brd, robot.sch]
2022-02-02 Renaming project on silkscreen
    [robot.brd]
2022-02-02 Frame DXF
    [frame.dxf]
2022-02-07 Updating mechanics
    [coupler.stl, motorbox_bottom.stl, motorbox_top.stl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]
2022-02-07 Adding DXFs
    [electronics_board.dxf, kicker_tip_1.dxf, kicker_tip_2.dxf]
2022-02-07 Updating motorbox top stl
    [motorbox_top.stl]
2022-02-08 Marker small fix
    [marker.dxf]
2022-02-09 Enforcing bounding values for power in kick
2022-02-15 LEDs, buzzer (wip)
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2022-02-16 Allowing power in kick command
2022-02-16 Checking voltage, alerting when it is too low
    [buzzer.cpp, config.h, main.cpp]
2022-02-16 Fixing awful float/int conversion
    [motors.cpp]
2022-02-16 PWM set to 0 when target speed is 0
2022-02-17 Using Arduino 2.0.2 and Ticker
2022-02-17 Fixing "old" firmware version detection
    [robot.py]
2022-02-18 Electronic fixes
    [robot.brd, robot.sch]
2022-02-18 Using Arduino-ESP32 2.0.2 as dependency
2022-02-18 Rev1 routed
    [robot.brd, robot.sch]
2022-03-22 Vision Speed Update + Fix Resolution problem
    [detection.py, field.py, game_controller.py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]
2022-03-25 Upgrading capacitors to 3300uF
    [robot.brd, robot.sch]
2022-04-08 Game Start/Stop/Pause logic and UX + Calibrate Field button + define 8 threads for waitress
2022-04-11 Added Timer backend and frontend + Fixed the fact that arUco square appears under drawn field lines
    [backend.py, detection.py, referee.py]
2022-04-15 Add Camera Height to compute positions of robot and ball (Thales version) (backend+frontend)
2022-04-19 Fixing VIN arrival on U5
    [robot.brd]
2022-04-22 Changing the way voltage is smoothed, allowing lower voltages
2022-04-22 New Camera Calibration + Preemption update
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2022-04-23 Removing now useless camera height
2022-04-23 Enhancing render of camera settings
2022-04-23 Removing @api.slot, using type hinting and inspection instead
2022-04-26 Huge Referee Update -> all get Fonction in one (game_state dict) + Display prempt reason + referee minor fixes
    [backend.py, control.py, detection.py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]
2022-04-26 Goal validation implemented + Swap cover placement + HalfTime Preemption + Force place robot preemption
    [backend.py, client.py, control.py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]
2022-04-27 Major Referee Update (missing 3s next to ball + sending state of game for clients)
    [client.py, detection.py, referee.py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]
2022-05-03 Preemption bugfix + referee adaptation
    [control.py, referee.py, tasks.py]
2022-05-03 Fixing setting back a marker to none, using CSS instead of JSS for capitalization
    [backend.py]
2022-05-04 Restoring LEDs after blinking
2022-05-04 Fixing timer for referee events
    [referee.py]
2022-05-04 Fixing and factorizing wait ball placement
    [referee.py]
2022-05-04 Disabling motors after 3s of inactivity
2022-05-04 Fixing available robots check
    [tasks.py]
2022-05-04 New 16cm field markers
2022-05-06 Using a helper for resetting LEDs
    [robots.py]
2022-05-10 Adding 1uF decoupling for motors
    [robot.brd, robot.sch]
2022-05-11 Electronics BOM
    [BOM.xlsx]
2022-05-11 Updating 3D parts
    [wheel.stl, wheel1.stl, wheel2.stl]
2022-05-11 New markers
    [marker.dxf]
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2022-05-12 Using a thread to ensure safety of detection infos while processing it in referee
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2022-05-13 Using a fix focale length
    [constants.py, field.py, video.py]
2022-05-13 Using logger instead of print() while outputing identify infos
2022-09-01 Re-routed electronics (not tested)
    [robot.brd, robot.sch]
2022-09-01 Slight shift
    [robot.brd]
2022-09-01 Little tweaks on connector's wiring
    [robot.brd]
2022-09-02 Electronics rework wip
    [BOM.xlsx, robot.brd, robot.sch]
2022-09-16 Updating firmware to new board revision
2022-09-16 Adding 5k pulling resistor between M1A and M1B
    [robot.brd, robot.sch]
2022-09-16 RSK rev2
    [robot.brd, robot.sch]
2022-09-16 Re-camming, minor renamings
    [robot.brd, robot.sch]
2022-09-16 Sheet titles
    [robot.sch]
2022-09-16 Updating BOM
    [BOM.xlsx]
2022-09-16 Updating BOM and ordering informations
    [BOM.xlsx]
2022-09-17 Updating STL files
    [wheel1.stl, wheel2.stl]
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2022-11-09 Creating penalty locations (fixes #66)
    [referee.py]
2022-11-10 Add time to clear the penalty spot (fixes #66)
    [referee.py]
2022-11-14 Client exceptions management (fixes #70)
    [client.py]
2022-11-15 Add logging to Client and add new option for exceptions managements (fixes #70)
    [client.py, control.py]
2022-11-15 Reset timer with Start Game (fixes #72)
    [referee.py]
2022-11-15 Add a more visible alert for timer end
2022-11-17 correct color to penalty annotations
    [detection.py]
2022-11-27 Schematics update
    [robot.sch]
2022-11-27 DXL & Steps for kicker tip
    [kicker_tip_1.dxf, kicker_tip_1.step, kicker_tip_2.dxf]
2022-11-27 Kicker tips
    [kicker_tip_1.dxf]
2022-12-05 Adding D2
    [BOM.xlsx]
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2022-12-05 Adding D2 diode
    [robot.brd, robot.sch]
2022-12-21 Adjusting ADC (to investigate further)
2023-01-28 start of the simulator without collision real mode not works
    [backend.py, client.py, game_controller.py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]
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2023-02-08 fix the simulated kick and merge simulated Detection and Video
    [backend.py, simulator.py]
2023-03-07 add remove button for offline robots
2023-03-20 Add teleport, beep and leds to clients
2023-03-20 patch collision and kick issue
    [control.py, simulator.py]
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2023-03-24 Better handling of collisions
    [backend.py, client.py, constants.py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]
2023-03-28 Add leds to simulator
2023-04-03 add ball replacement indicator in simulator
    [backend.py, client.py, referee.py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]
2023-04-29 Camera view should be updated anyway in the Video tab
2023-05-02 camera run before simulated view
2023-05-15 Start timer after ball placement after half time
2023-05-15 increase distance for swap cover
    [client.py]
2023-05-21 Detail in BOM
    [BOM.xlsx]
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2023-11-10 Led and buzzer when swapping covers placement
    [backend.py, referee.py, tasks.py]
2024-04-10 Update ESP32Encoder from 0.8.0 to 0.10.2 (cause old version unvailable)
2024-04-11 Adding F-shaped batteries blocker
    [blocker.stl]
2024-05-21 Fixing kick() prototype in abstract class
    [robot.py]
2024-06-03 Fixing wheel rotate detection, locking when a packet was received
    [com.cpp, config.h]
2024-06-04 Fixing extra timeout for cameras api call
2024-06-15 Adding RS1M footprint (wip)
    [robot.brd, robot.sch]
2024-07-01 Not switching to BT if motors were enabled
2024-07-01 Updating com.cpp accordingly to motors.cpp
2024-07-01 Some more comments, making PWM positive by defaults (fixes two -1)
    [config.h, motors.cpp]
2024-09-30 Optimizing sim rendering (switching robots to SVG, using only one canvas for robots, using off-screen rendering)
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2024-10-21 Adding --reset flag to reset the configuration
    [game_controller.py]
2025-02-26 Using current location instead of hard-coded 127 for APIBackend
2025-04-11 Adding slight foreseeing for collisions avoidance
    [client.py]
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2025-09-26 Fixing kicker_tip_1 dimension scale
    [kicker_tip_1.dxf]
2025-10-09 Robot & BOM rev3
    [BOM.xlsx, robot.brd, robot.sch]
2025-10-09 BOM rev3
    [BOM.xlsx]
2025-11-05 Adding an extra test on led size
2025-11-08 Ruff format, threads to daemon
2025-11-08 Running ruff check --fix
    [backend.py, control.py, field.py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]
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2026-03-15 Avoiding annoying switch between views
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2026-05-03 having robots knowing their led states + fixes
    [backend.py, control.py, detection.py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]
2026-05-28 Switching to Python logger, changing logic to start/stop logs
2026-06-01 began fix for enabling recording input
    [backend.py]
2026-06-01 synced rec-settings input with back, and set replay at the first frame where robots are visible when initializing replay mode

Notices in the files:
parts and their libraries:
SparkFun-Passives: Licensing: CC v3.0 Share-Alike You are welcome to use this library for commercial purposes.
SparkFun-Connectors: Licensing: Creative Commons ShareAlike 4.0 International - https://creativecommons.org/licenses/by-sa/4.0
